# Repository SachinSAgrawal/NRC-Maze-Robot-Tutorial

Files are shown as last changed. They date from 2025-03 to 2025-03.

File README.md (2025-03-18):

# NRC Maze Robot Tutorial

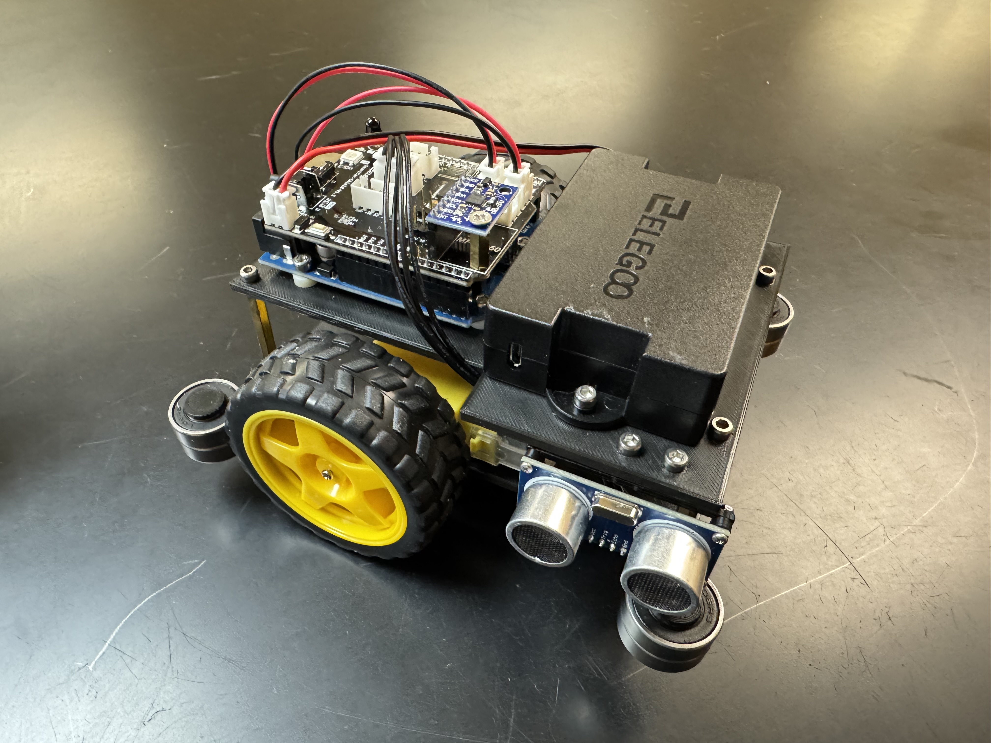
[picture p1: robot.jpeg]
robot


## About
I was going to participate in the National Robotics Challenge as part of my high school’s Engineering Team, which I lead until something happened. However, I am making this tutorial under the CC BY-NC-ND license so that the designs and code are accessible to anyone. If you used this tutorial or found it helpful, I would appreciate if you starred it or even shared it with your friends.

## Competition
The [National Robotics Challenge](https://www.thenrc.org/) takes place each Spring in Marion, Ohio. There are multiple different contests with different levels of difficulty. This tutorial is specifically for the Robot Maze Contest, which involves building and programming a robot to navigate a right/left turn maze. The maze is 10 segments by 10 segments, with each segment being 10 inches by 10 inches. However, the internal navigable is 9.25 inches because the walls have width. The robot must be no larger than 7x7x7 inches and must be completely autonomous (no remote controls or tethers). It must be in contact with the ground at all times and has up to five minutes to complete a run, where faster is better.

## Robot Information
This robot meets those design criteria, and uses an Arduino Uno as it's microcontroller. It can basically be made out of parts from the [ELEGOO Smart Robot Car Kit V4.0](https://www.amazon.com/ELEGOO-Tracking-Ultrasonic-Intelligent-Educational/dp/B07KPZ8RSZ), with everything else being 3D printed or quite inexpensive. The robot moves forward through each segment one at a time, which ensures that it is centered before executing a turn. When it does execute a turn, wherever possible, it moves forward until it is square with the wall and then backs up to do the turn. This realignment functionality helps minimize drift. The robot also checks if all turns are accurate using the MPU, and if that is not the case, then the robot self-corrects. For long stretches of wall that are on the right side of the robot, it can use a PD controller to hug that wall.

## Code Explanation
The only function that is not used is the `mpuAngles` one, which prints all three axes to Serial. Other than that, every line of the code is necessary for the robot to work properly. The first part of the code handles all the variable definitions, followed by the `setup` for things like pin modes. Then there is the main `loop` function, which detects if the button is pressed, and if so, starts doing the maze logic. The rest of it is organized into a bunch of sections with each section containing a few related helper functions for moving, reading from sensors, etc. This is also where the PD controller and check turn function live. The code is fully commented, so you should have no trouble understanding it, and if you can't, then your coding skills are probably not good enough to be competing in the first place.

## Robot Tutorial
Print out the top plate, bottom plate, bearing stoppers, and both ultrasonic mounts according to the specified [print settings](printSettings.md). All five files are in the `printedParts` folder, as well as on both [Printables](https://www.printables.com/model/1232178) and [Thingiverse](https://www.thingiverse.com/thing:6981409). Then, check out the [parts list](partsList.md) and make sure you have everything else. Next, read the [instructions](instructions.md) to assemble your robot. Lastly, upload the [code](mazeCode/mazeCode.ino) onto the Arduino to finish your robot. It is currently set to the maze layout for 2025. However, it is really easy to modify. It basically works like block coding, where you just need to call each function sequentially to have the robot move forward through one segment or turn.

## Notes

### Pictures
This tutorial currently does not include any pictures besides the ones in the parts list and at the top of this file. I will update it with them as soon as possible so that it is easier to follow.

### Crediting
As part of the license included in this repository (see below), you must credit me in your Engineer's Notebook. It would be dishonest and unethical to pass this off as your own because you didn't do the work.

### LED
The LED on the shield indicates the status of the robot. It will be red while the robot is getting set up and turn green once the robot is ready. It is super important to not move the robot in that time, as the MPU is being calibrated. Once the code is finished running, the LED will turn white. While it is moving, the LED will be yellow, teal, or purple if it is going forward, turning, or waiting, respectively. Once the code has run once, it must be reset using the button to run it again.

## Contributors
Sachin Agrawal: I'm a self-taught programmer who knows many languages and I'm into app, game, and web development. For more information, check out my website or Github profile. If you would like to contact me, my email is [github@sachin.email](mailto:github@sachin.email).

## License
This package is licensed under the [Creative Commons BY-NC-ND License](LICENSE.txt). For more information, please visit their [website](https://creativecommons.org/share-your-work/use-remix/cc-licenses/#by-nc-nd). I am only giving everyone permission to edit the layout of the maze since it changes each year, and delay timings as needed. Otherwise, please respect the No Derivatives part of the license and do not alter any of the remaining code. This means that you are not allowed to put this code into ChatGPT to change it in any way. This also means that you cannot write a library to try to shorten this code because, on top of being a bad idea, you are actually making the code longer, but splitting it across multiple files. It is also prohibited to modify any of the printed parts, including removing my name from the top plate. Unless I have explicitly given you permission in writing to make more modifications, what is said here takes precedence in terms of licensing.

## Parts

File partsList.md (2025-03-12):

# Parts List

ELEGOO Smart Robot Car Kit V4.0: https://www.amazon.com/ELEGOO-Tracking-Ultrasonic-Intelligent-Educational/dp/B07KPZ8RSZ

| Name | Quantity | Image | Status | Link | Reference | Docs | Pinout | Shield |
|---|---|---|---|---|---|---|---|---|
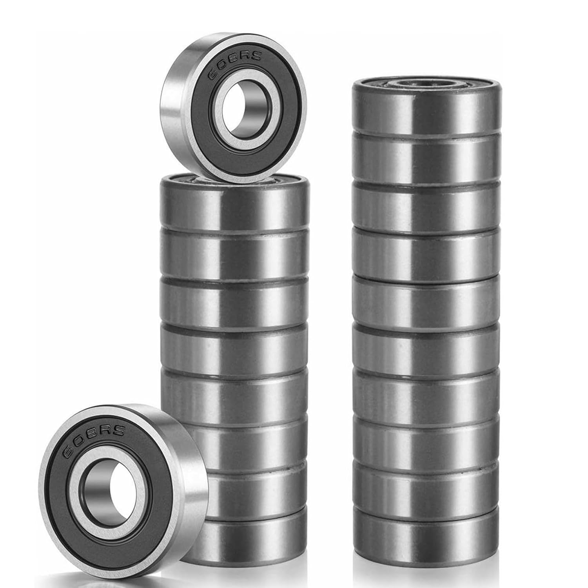
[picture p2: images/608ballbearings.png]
| 608 Ball Bearings | 1 pack of 25 |  | Separate | [Amazon](https://www.amazon.com/YAMASO-Pcs-608-Ball-Bearings/dp/B0CYYYZRV9) | | | | |
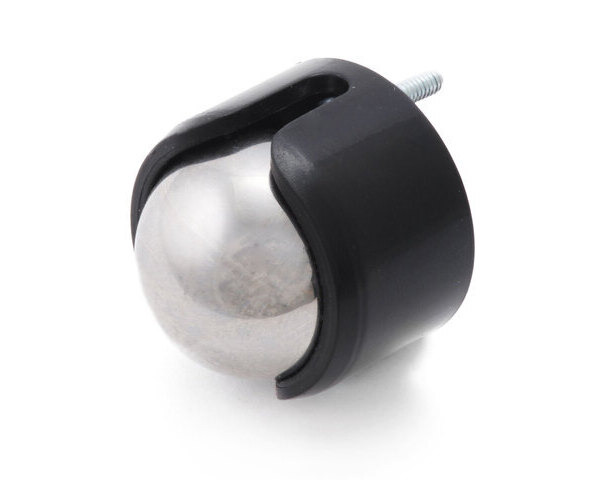
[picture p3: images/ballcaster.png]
| Ball Caster with 3/4″ Metal Ball | 1 |  | Separate | [Pololu](https://www.pololu.com/product/955) | Holes 15mm apart | | | |
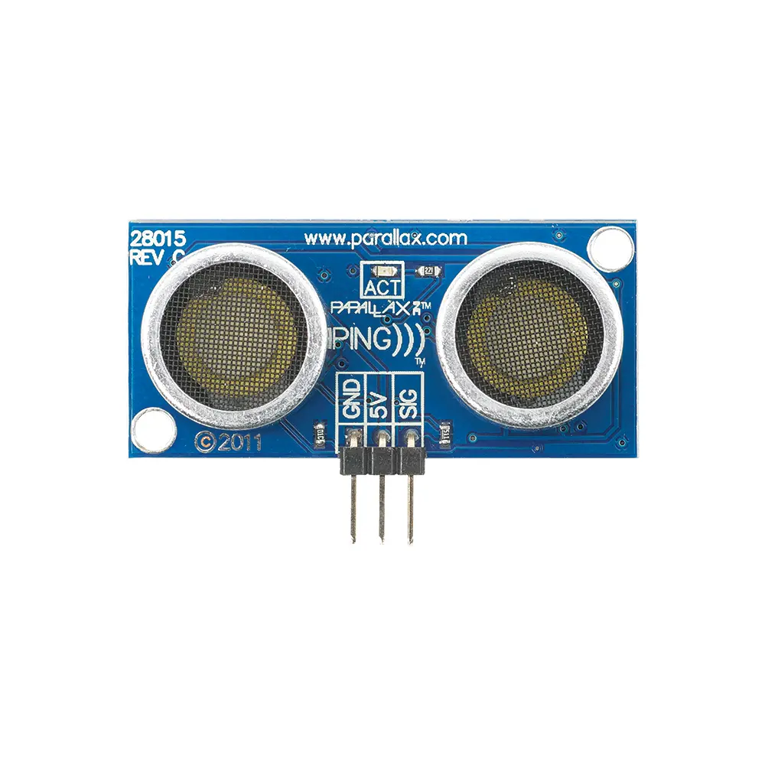
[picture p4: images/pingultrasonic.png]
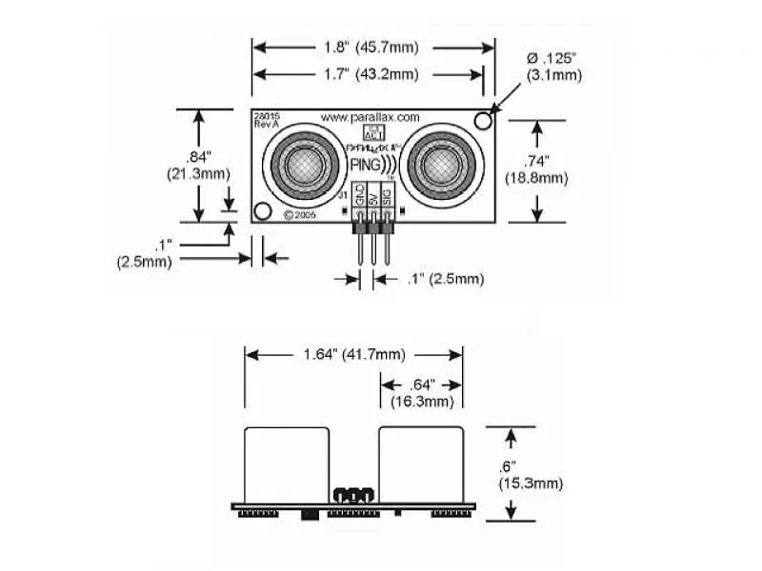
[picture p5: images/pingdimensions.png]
| Parallax Ping))) Ultrasonic Sensor  | 1 |  | Separate | [Parallax](https://www.parallax.com/product/ping-ultrasonic-distance-sensor/) |  | [Arduino](https://docs.arduino.cc/built-in-examples/sensors/Ping/) | Gnd, 5V, Signal | Servo2 |
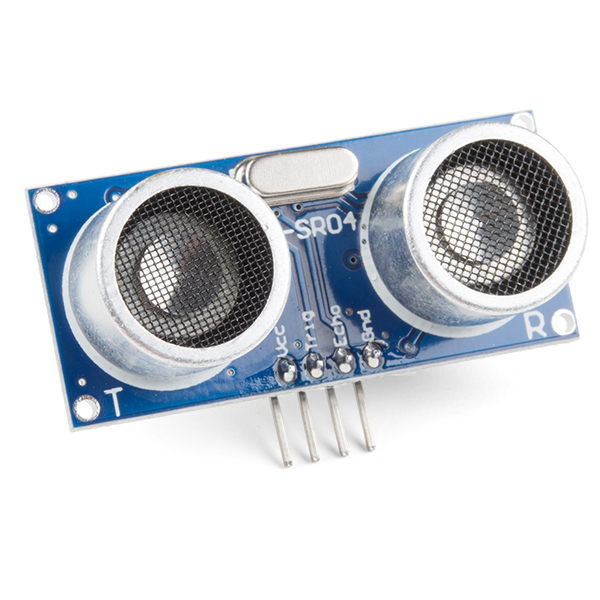
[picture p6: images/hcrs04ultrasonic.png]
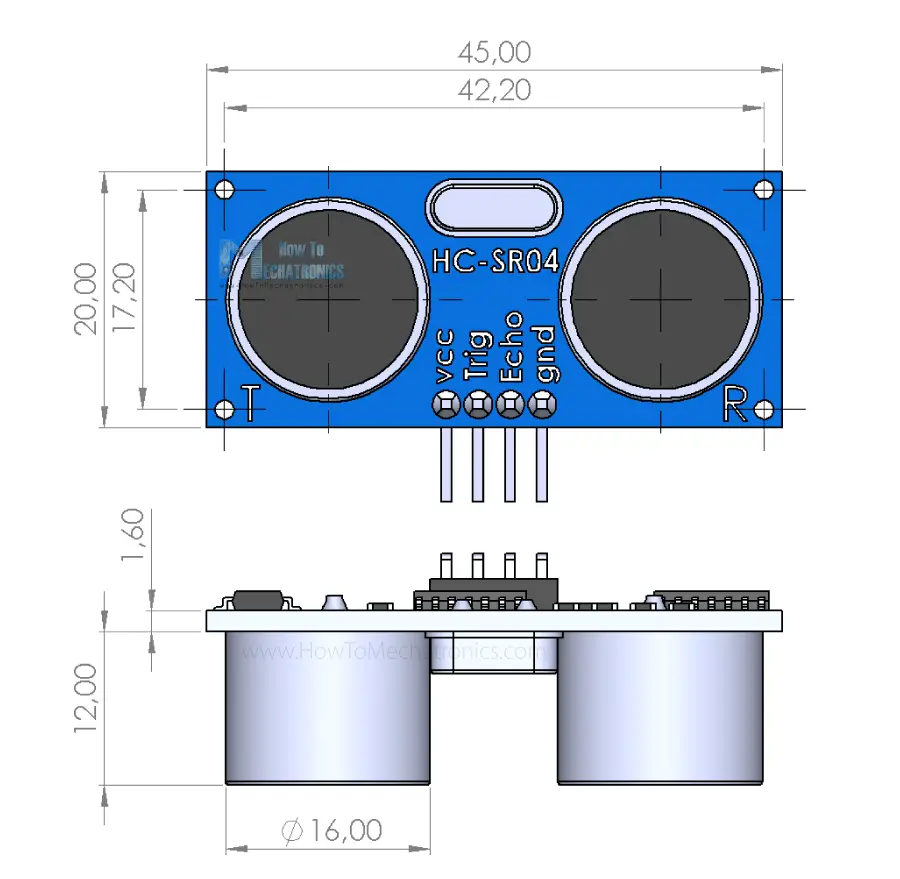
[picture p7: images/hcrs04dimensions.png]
| HC SR04 Ultrasonic Sensor | 1 |  | From Elegoo Kit | |   | | Vcc, Trig (Digital), Echo (Digital), Gnd | US |
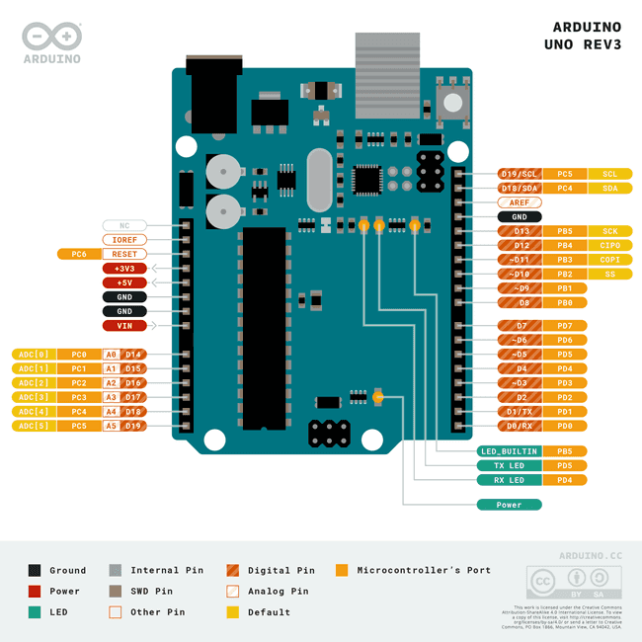
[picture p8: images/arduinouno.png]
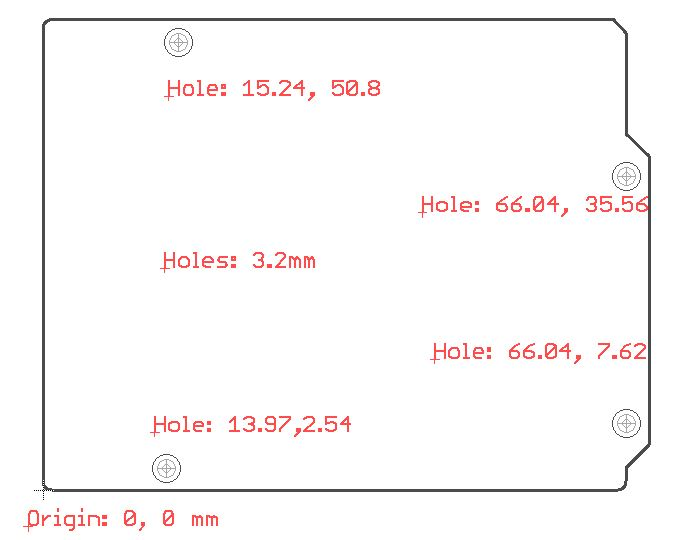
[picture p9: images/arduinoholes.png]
| Arduino Uno | 1 |  | From Elegoo Kit | |  | | | |
| Smart Robot Car Kit Shield | 1 |  | From Elegoo Kit | | | [Google Drive](https://drive.google.com/drive/folders/1OGWDPXKMALmwXZrCxrwO-zCWzvXuK-5q) | | |
| MPU 6050 Gyroscope | 1 |  | From Elegoo Kit | |  | | Vcc, Gnd, SCL, SDA | MPU |
| TT DC Gearbox Motor | 2 |  | From Elegoo Kit | | | | Pos, Neg | M1 & M2  |
| Rubber Tire and Wheel | 2 |  | From Elegoo Kit | | | | | |
| Battery Pack with JST Connector | 1 |  | From Elegoo Kit | | Holes 78mm apart | | Vin, Gnd | Power_In |
| M3 40mm Threaded Hexagon Spacers | 4 |  | From Elegoo Kit | | | | | |
| M3 Hex Nuts | 15 |  | From Elegoo Kit | | | | | |
| Aluminum Blocks | 2 |  | From Elegoo Kit | | | | | |
| M3 10mm Hex Screws | 16 |  | From Elegoo Kit | | | | | |
| M3 12mm Hex Screws | 2 |  | From Elegoo Kit | | | | | |
| M3 14mm Hex Screws | 5 |  | From Elegoo Kit | | | | | |
| M3 30mm Hex Screws | 4 |  | From Elegoo Kit | | | | | |
| Separation Pillars | 5 |  | From Elegoo Kit | | | | | |
| M3 5mm Countersunk Screws | 2 |  | From Elegoo Kit | | | | | |
| M3 11mm Copper Pillar | 1 |   | From Elegoo Kit | | | | | |
| M1.6 8mm Screws | 4 |  | From Elegoo Kit | | | | | |
| M1.6 Nuts | 4 |  | From Elegoo Kit | | | | | |
| M2 25mm Self-Tapping Screws | 2 |  | From Elegoo Kit | | | | | |
| 4 Pin JST Cable | 1 |  | From Elegoo Kit | | | | | |
| 3 Pin Jumper | 1 |  | Separate | | | | | |
| Top Plate | 1 |  | 3D Print | | | | | |
| Bottom Plate | 1 |  | 3D Print | | | | | |
| Bearing Stoppers | 4 |  | 3D Print | | | | | |
| Ultrasonic Mount 1 | 1 |  | 3D Print | | | | | |
| Ultrasonic Mount 2 | 1 |  | 3D Print | | | | | |

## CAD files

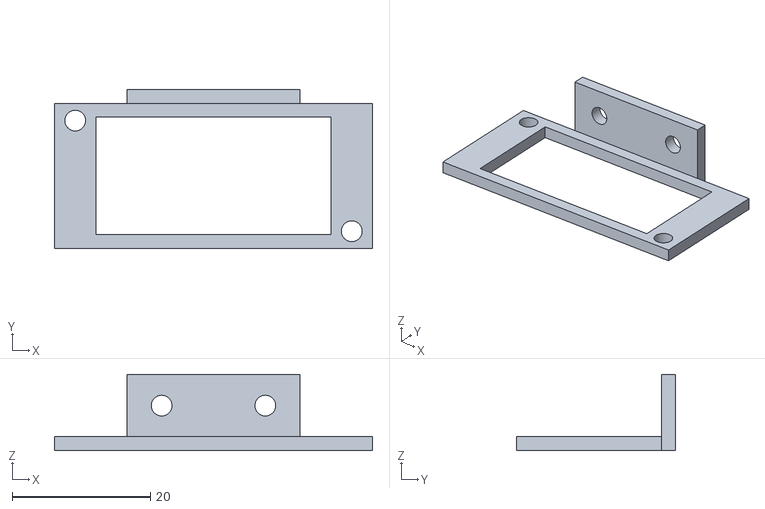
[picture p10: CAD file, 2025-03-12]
printedParts/ultrasonicmount1.stl
46.0 x 23.0 x 11.0

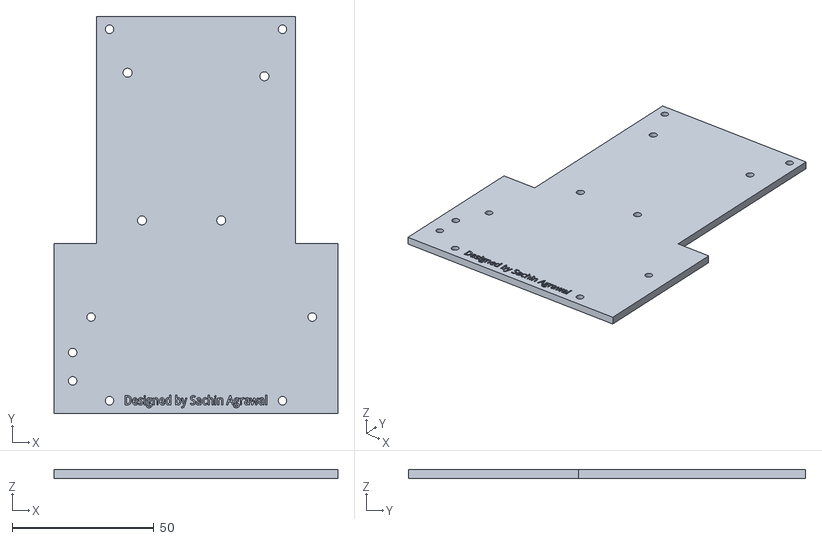
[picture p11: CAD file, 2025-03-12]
printedParts/topplate.stl
100.0 x 140.0 x 3.00

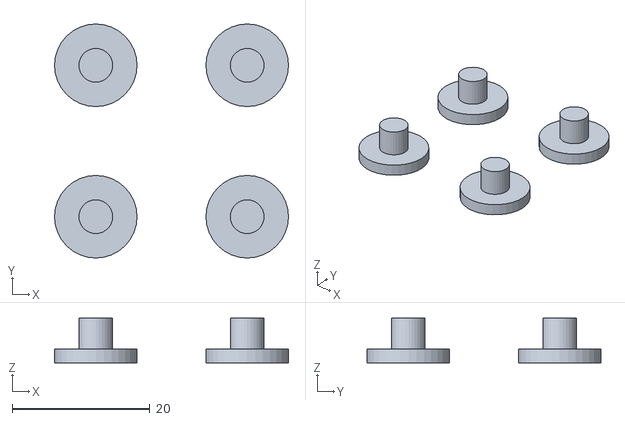
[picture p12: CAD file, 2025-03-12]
printedParts/bearingstoppers.stl
34.0 x 34.0 x 6.50

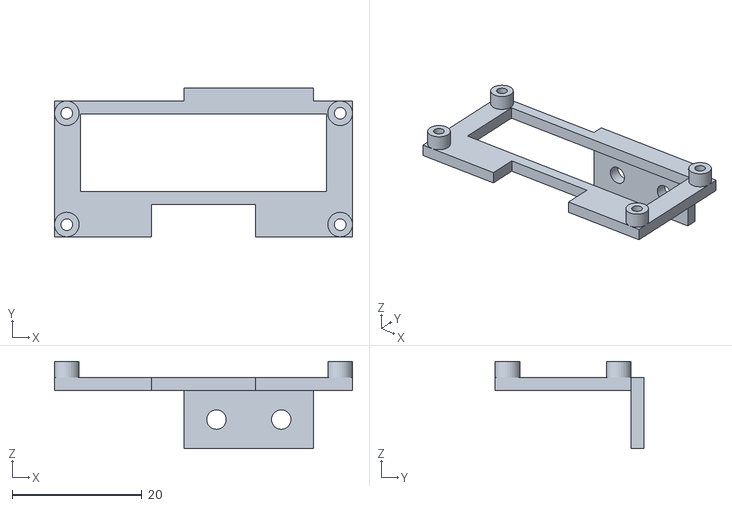
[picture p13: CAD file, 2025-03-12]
printedParts/ultrasonicmount2.stl
46.0 x 23.0 x 13.5

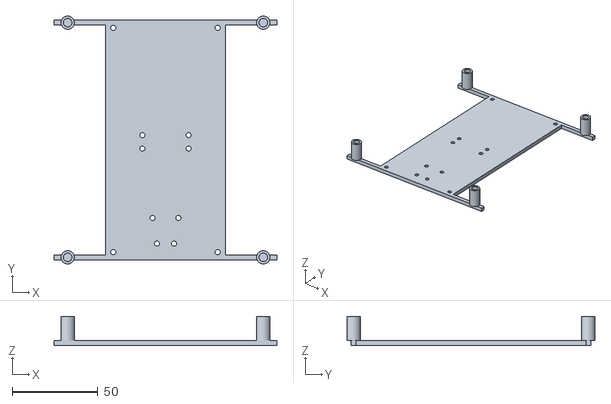
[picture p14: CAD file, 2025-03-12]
printedParts/bottomplate.stl
130.0 x 144.8 x 17.0

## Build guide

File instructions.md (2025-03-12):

# Instructions

## Step 1
Slide two bearings onto each of the four posts on the bottom plate.

## Step 2
Apply a little bit of super glue to the bearing stoppers and attach them to the tops of the bearing holders to prevent the bearings from sliding out if the robot is turned upside down.

## Step 3
Screw the aluminum mounting blocks onto the motors using two M3 30mm screws and two M3 hex nuts. Repeat this twice.

## Step 4
Attach both motors onto the bottom plate using four M3 10mm screws. 

## Step 5
Screw the ball caster into the bottom plate using the nuts/bolts that came with it, then slide the metal ball into the caster.

## Step 6
Screw the Ping ultrasonic sensor into the first mount using two M3 14mm screws with two separation pillars and two M3 hex nuts.

## Step 7
Attach that assembly to the bottom plate using two M3 10mm screws and two M3 hex nuts. 

## Step 8
Screw the HC-SR04 ultrasonic sensor into the second mount using four M1.6 8mm screws and four M1.6 nuts.

## Step 9
Attach that assembly to the top plate using two M3 10mm screws and two M3 hex nuts. 

## Step 10
Screw the battery pack into the top plate using two M3 12mm screws and two M3 hex nuts. 

## Step 11
Screw the Arduino Uno to the top plate using three M3 14mm screws with three separation pillars and three M3 hex nuts.

## Step 12
Attach the MPU to the shield, then screw it in place using the M3 5mm countersunk screws and M3 11mm copper pillar.

## Step 13
Attach the shield to Arduino by sliding it on.

## Step 14
Screw the M3 40mm spacers to the bottom plate using four M3 10mm screws.

## Step 15
Attach the top plate to the tops of the spacers using four M3 10mm screws.

## Step 16
Connect all of the wires according to the `Shield` column in the [parts list](partsList.md).

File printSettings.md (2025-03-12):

# Print Settings

I printed all parts on a Prusa i3 MK3S+, but any printer with good tolerances should work. Depending on how well your bed adhesion is, you may or may not want to add glue, especially for the top and bottom plates.

## All Parts
- 3 Perimeters
- 50% Infill 
- Gyroid Pattern
- 0.2mm Layer Height

## Part Specific

### Top Plate
- No Supports Needed
- Brim Enabled

### Bottom Plate
- Support (on build plate only)
- Brim Enabled

### Ultrasonic Mount 1
- No Supports Needed
- Brim Optional

### Ultrasonic Mount 2
- Support (on build plate only)
- Brim Enabled

### Bearing Stoppers
- No Supports Needed
- Brim Disabled

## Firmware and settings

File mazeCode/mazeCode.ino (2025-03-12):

// VARIABLES

// How long to wait after each instruction
int delayLength = 500;

// How long to make a 90 degree turn
int turnNinetyL = 350;
int turnNinetyR = 350;

// How long to go forward 10 inches
int forwardTenIn = 450;

// How long to hit into wall to realign
int forwardToClear = 250;

// How far to back up after realigning
int backFromRealign = 150;

// DEFINITIONS

// Button
#define button 2
boolean buttonState;
boolean buttonPressed;
boolean codeHasRun = false;

// RGB LED
#include "FastLED.h"
#define PIN_RBGLED 4
#define NUM_LEDS 1
CRGB leds[NUM_LEDS];

// Needed for LED but do not understand it fully
uint32_t Color(uint8_t r, uint8_t g, uint8_t b) {
  return (((uint32_t)r << 16) | ((uint32_t)g << 8) | b);
}

// Front Ultrasonic
const int pingPin = 11;
long durationF;
float distanceF;

// Right Ultrasonic
const int trigPinR = 13;
const int echoPinR = 12;
long durationR;
float distanceR;

// MPU6050
#include "Wire.h"
#include <MPU6050_light.h>
MPU6050 mpu(Wire);
float angZ = 0;

// DC motors
#define PWMA 5
#define PWMB 6
#define BIN1 7
#define AIN1 8
#define STBY 3

// Robot Speed
int speedMed = 125; 
int speedFast = speedMed + 50; 
int speedSlow = speedMed - 50;
int motorACorrection = 4;

// PD Controller
#define goalR 2 // 2 inches away from right wall
const float Gp = 30.0; 
const float Gd = 60.0;
int leftPWM = speedMed;
int rightPWM = speedMed;
float errorP; // Proportional error
float errorD; // Derivative error
float initialPoint; 
float finalPoint;

// Important setup function
void setup() {
  // Set up the LED
  FastLED.addLeds<NEOPIXEL, PIN_RBGLED>(leds, NUM_LEDS);
  FastLED.setBrightness(10); // Don't increase because it gets too bright

  // Warning during setup
  FastLED.showColor(Color(255, 1, 1)); // Red

  // Start communication with the serial monitor
  Serial.begin(9600);

  // Enable the right ultrasonic sensor
  pinMode(trigPinR, OUTPUT); 
  pinMode(echoPinR, INPUT);

  // Set up the button pin
  pinMode(button, INPUT_PULLUP); 

  // Set up the DC motors
  pinMode(PWMA, OUTPUT);
  pinMode(PWMB, OUTPUT);
  pinMode(AIN1, OUTPUT);
  pinMode(BIN1, OUTPUT);
  pinMode(STBY, OUTPUT);

  // Set the initial motor speed
  motorSpeed(speedSlow);

  // Set up the MPU
  Wire.begin();
  byte status = mpu.begin();
  Serial.print(F("MPU6050 status: "));
  Serial.println(status);
  while(status!=0){ } // Stop everything if could not connect to it
  Serial.println("Calculating offsets, do not move MPU6050");
  delay(1000);
  mpu.calcOffsets(); // Gyro and accelerometer
  Serial.println("Ready");

  // Setup complete
  FastLED.showColor(Color(1, 255, 1)); // Green
}

// Important loop function
void loop() {
  // Determine whether the button is pressed
  buttonState = digitalRead(button);

  if (buttonState == 0) {
    // Button has been pressed
    FastLED.showColor(Color(1, 1, 255)); // Blue

    // Can execute main logic if it is not already run
    if (!codeHasRun) {
      // WEEEEEE
      mazelogic2025();

      codeHasRun = true;
      Serial.println("Code Has Run");
      FastLED.showColor(Color(255, 255, 255)); // White
    }
  } else if (codeHasRun) {
    // Code has run once before
    FastLED.showColor(Color(255, 255, 255)); // White
  }
}

// Functions for the logic of the different mazes 

// Full 100'x100' maze
void fullMazeLogic() {
  // =========
  // EDIT THIS
  // =========
}

// The maze layout from 2025
void mazelogic2025() {
  tenInForward();
  tenInForward();
  tenInForward();
  // 4
  turnLeft();
  tenInForward();
  tenInForward();
  // 6
  turnLeft();
  tenInForward();
  // 7
  turnRight();
  tenInForward();
  // 8
  turnLeft();
  tenInForward();
  // 9
  turnRight();
  tenInForward();
  // 10
  turnRight();
  tenInForward();
  tenInForward();
  // 12
  ninetyRight();
  tenInForward();
  // 13
  turnLeft();
  tenInForward();
  // 14
  turnRight();
  tenInForward();
  tenInForward();
  tenInForward();
  // 17
  turnLeft();
  tenInForward();
  tenInForward();
  // 19
  turnLeft();
  tenInForward();
  tenInForward();
  tenInForward();
  // 22
  ninetyRight();
  tenInForward();
  tenInForward();
  // 24
  ninetyLeft();
  tenInForward();
  tenInForward();
  // 26
  turnLeft();
  tenInForward();
  tenInForward();
  // 28
  turnRight();
  tenInForward();
  // 29
  turnLeft();
  tenInForward();
  // 30
  turnRight();
  tenInForward();
  // 31
  turnLeft();
  tenInForward();
  // 32
  turnRight();
  tenInForward();
  // 33
  turnRight();
  tenInForward();
  hugWallUntil(12);
  tenInForward();
  // 38
  turnLeft();
  tenInForward();
  // 39
  turnLeft();
  hugWallUntil(2);
}

// Functions to continuously update the MPU when the robot is moving

// Actual logic
void dddelay(int dTime) {
  long currTime = millis();
  while (millis() - currTime < dTime) {
    mpu.update();
    angZ = mpu.getAngleZ();
    delay(5);
  }
}

// Also update LED
void ddelay(int dTime) {
  FastLED.showColor(Color(255, 1, 255)); // Magenta
  dddelay(dTime);
  FastLED.showColor(Color(0, 0, 0)); // Off
}

// Functions to set the motor speed

// Set both speeds
void motorSpeed(int speed) {
  int constrainedSpeed = constrain(speed, speedSlow, speedFast);
  motorASpeed(constrainedSpeed);
  motorBSpeed(constrainedSpeed);
}

// Independently set X
void motorASpeed(int speed) {
  analogWrite(PWMA, speed + motorACorrection);
}

// Independently set Y
void motorBSpeed(int speed) {
  analogWrite(PWMB, speed);
}

// Functions to have the robot move in a certain direction for a specified time

// Forward
void moveForward(int milliseconds) {
  FastLED.showColor(Color(255, 255, 1)); // Yellow
  digitalWrite(STBY, HIGH);
  digitalWrite(AIN1, HIGH);
  digitalWrite(BIN1, HIGH);
  // Ease in and out for longer distances
  if (milliseconds == forwardTenIn) {
    for (int i = 0; i <= 25; i++) {
      motorSpeed(speedSlow + 2 * i);
      dddelay(5);
    }
    motorSpeed(speedMed);
    dddelay(milliseconds - 250);
    for (int i = 0; i <= 25; i++) {
      motorSpeed(speedMed - 2 * i);
      dddelay(5);
    }
  } else {
    dddelay(milliseconds);
  }
  motorSpeed(speedSlow);
  FastLED.showColor(Color(0, 0, 0)); // Off
  digitalWrite(STBY, LOW);
}

// Backward
void moveBackward(int milliseconds) {
  FastLED.showColor(Color(255, 255, 1)); // Yellow
  digitalWrite(STBY, HIGH);
  digitalWrite(AIN1, LOW);
  digitalWrite(BIN1, LOW);
  dddelay(milliseconds);
  FastLED.showColor(Color(0, 0, 0)); // Off
  digitalWrite(STBY, LOW);
}

// Left
void moveLeft(int milliseconds) {
  FastLED.showColor(Color(1, 255, 255)); // Teal
  digitalWrite(STBY, HIGH);
  digitalWrite(AIN1, LOW);
  digitalWrite(BIN1, HIGH);
  dddelay(milliseconds);
  FastLED.showColor(Color(0, 0, 0)); // Off
  digitalWrite(STBY, LOW);
}

// Right
void moveRight(int milliseconds) {
  FastLED.showColor(Color(1, 255, 255)); // Teal
  digitalWrite(STBY, HIGH);
  digitalWrite(AIN1, HIGH);
  digitalWrite(BIN1, LOW);
  dddelay(milliseconds);
  FastLED.showColor(Color(0, 0, 0)); // Off
  digitalWrite(STBY, LOW);
}

// Turning functions that realign the robot each time

// Align and turn left
void turnLeft() {
  // Move forward until it hits the wall
  Serial.println("Forward");
  moveForward(forwardToClear);
  ddelay(delayLength);

  // Back up a little to clear the turn
  Serial.println("Back");
  moveBackward(backFromRealign);
  ddelay(delayLength);

  // Get the goal value to pass into function below
  mpu.update();
  float initAngle = mpu.getAngleZ();
  Serial.print("AngZ: ");
  Serial.println(initAngle);

  // Execute the actual turn
  Serial.println("Left");
  moveLeft(turnNinetyL);
  ddelay(delayLength);  

  // Check if the turn is accurate using goal
  Serial.println("Check Turn");
  checkAccurateTurn(initAngle, true, false);
  ddelay(delayLength);
}

// Align and turn right
void turnRight() {
  // Move forward until it hits the wall
  Serial.println("Forward");
  moveForward(forwardToClear);
  ddelay(delayLength);

  // Back up a little to clear the turn
  Serial.println("Back");
  moveBackward(backFromRealign);
  ddelay(delayLength);

  // Get the goal value to pass into function below
  mpu.update();
  float initAngle = mpu.getAngleZ();
  Serial.print("AngZ: ");
  Serial.println(initAngle);

  // Execute the actual turn
  Serial.println("Right");
  moveRight(turnNinetyR);
  ddelay(delayLength);

  // Check if the turn is accurate using goal
  Serial.println("Check Turn");
  checkAccurateTurn(initAngle, false, true);
  ddelay(delayLength);
}

// Turning functions that do not reset the robot each time

// Left 90 degrees
void ninetyLeft() {
  // Get the goal value to pass into function below
  mpu.update();
  float initAngle = mpu.getAngleZ();
  Serial.print("AngZ: ");
  Serial.println(initAngle);

  // Execute the actual turn
  Serial.println("Left 90 Deg");
  moveLeft(turnNinetyL);
  ddelay(delayLength);  

  // Check if the turn is accurate using goal
  Serial.println("Check Turn");
  checkAccurateTurn(initAngle, true, false);
  ddelay(delayLength);
}

// Right 90 degrees
void ninetyRight() {
  // Get the goal value to pass into function below
  mpu.update();
  float initAngle = mpu.getAngleZ();
  Serial.print("AngZ: ");
  Serial.println(initAngle);

  // Execute the actual turn
  Serial.println("Right 90 Deg");
  moveRight(turnNinetyR);
  ddelay(delayLength);  

  // Check if the turn is accurate using goal
  Serial.println("Check Turn");
  checkAccurateTurn(initAngle, false, true);
  ddelay(delayLength);
}

// Functions to just move forward/backward

// Move forward 10 inches through one maze segment
void tenInForward() {
  Serial.println("Forward 10in");
  moveForward(forwardTenIn);
  ddelay(delayLength);
}

// Move forward until a certain distance from front wall
void forwardUntil(int inches) {
  float distFromFrontWall;
  do {
    distFromFrontWall = frontUltrasonic();
    moveForward(50);
  } while (distFromFrontWall > inches);
  ddelay(delayLength);
}

// Move backward 10 inches through one maze segment
void tenInBackward() {
  Serial.println("Backward 10in");
  moveForward(forwardTenIn);
  ddelay(delayLength);
}

// Functions that can be called to easily read the ultrasonic sensors

// Front ultrasonic
float frontUltrasonic() {
  pinMode(pingPin, OUTPUT);
  digitalWrite(pingPin, LOW);
  delayMicroseconds(2);
  digitalWrite(pingPin, HIGH);
  delayMicroseconds(5);
  digitalWrite(pingPin, LOW);
  pinMode(pingPin, INPUT);
  durationF = pulseIn(pingPin, HIGH);
  distanceF = microsecondsToInches(durationF);
  Serial.print("DisF: ");
  Serial.println(distanceF, 2);
  return distanceF;
}

// Right ultrasonic
float rightUltrasonic() {
  digitalWrite(trigPinR, LOW);
  delayMicroseconds(2);
  digitalWrite(trigPinR, HIGH);
  delayMicroseconds(10);
  digitalWrite(trigPinR, LOW);
  durationR = pulseIn(echoPinR, HIGH);
  distanceR = durationR * 0.034 / 2.0 / 2.54;
  Serial.print("DisR: ");
  Serial.println(distanceR, 2);
  return distanceR;
}

// Ping conversion
long microsecondsToInches(long microseconds) {
  return microseconds / 74 / 2;
}

// Functions related to hugging aka staying a certain distance away from the right wall

// PD controller to move motors accordingly
void hugWall() {
  // Read and print the output of the right sensor
  Serial.println(" ");
  float distFromRightWall = rightUltrasonic();
  finalPoint = distFromRightWall; 

  // Just move straight if distance is greater than 200
  if (distFromRightWall > 200) {
    Serial.println("Going straight");
    motorSpeed(speedMed);
    moveForward(15);
    ddelay(10);
    return;
  }

  // Calculate and print the proportional and derivative errors
  errorP = distFromRightWall - goalR;  // Positive if too far and negative if too close to wall (should ideally be 0, with max of 2 and min of -2)
  errorD = finalPoint - initialPoint;  // Positive if heading away and negative if going towards wall (should be 0, with very slight variances)

  // Print the errors to the serial monitor
  Serial.print("ErrP: ");
  Serial.println(errorP);
  Serial.print("ErrD: ");
  Serial.println(errorD);

  // Print finalPoint and initialPoint to check if updating correctly
  Serial.print("Final: ");
  Serial.println(finalPoint, 2);
  Serial.print("Initl: ");
  Serial.println(initialPoint, 2);

  // Use proper math to calculate the wheel speed and print it
  leftPWM = (rightPWM + errorP * Gp + errorD * Gd);
  leftPWM = constrain(leftPWM, speedSlow, speedFast);
  Serial.print("lPWM: ");
  Serial.println(leftPWM);
  Serial.print("rPWM: ");
  Serial.println(rightPWM);

  // Actually move the wheels at that speed
  motorASpeed(rightPWM);
  motorBSpeed(leftPWM);
  moveForward(15);

  // Update the memory value
  initialPoint = finalPoint;

  ddelay(10);
}

// Hug the wall for a set amount of times
void hugWallfor(int count) {
  for (int i = 0; i < count; i++) {
    hugWall();
  }
  motorSpeed(speedSlow);
  ddelay(delayLength);
}

// Hug the wall until a certain distance from front wall
void hugWallUntil(int inches) {
  float distFromFrontWall;
  do {
    distFromFrontWall = frontUltrasonic();
    hugWall();
  } while (distFromFrontWall > inches);
  motorSpeed(speedSlow);
  ddelay(delayLength);
}

// Functions related to the MPU6050 gyroscope

// Print the MPU data to the serial monitor
void mpuAngles() {
  // Get angle variables
  mpu.update();
  float angX = mpu.getAngleX();
  float angY = mpu.getAngleY();
  float angZ = mpu.getAngleZ();

  // Print them
  Serial.print("X : ");
	Serial.print(angX);
	Serial.print("\tY : ");
	Serial.print(angY);
	Serial.print("\tZ : ");
	Serial.println(angZ);
}

// Check if the robot has turned the full 90 degrees and finish turning as needed
void checkAccurateTurn(float originalAngle, bool leftTurn, bool rightTurn) {
  // Calculate the angles
  float targetAngle = 0;

  if (leftTurn && !rightTurn) {
    targetAngle = originalAngle + 90;
  } else if (rightTurn && !leftTurn) {
    targetAngle = originalAngle - 90;
  }

  float tolerance = 1;
  float goalMore = targetAngle + tolerance;
  float goalLess = targetAngle - tolerance;

  // Print the angles
  Serial.print("Goal: ");
  Serial.println(targetAngle);
  Serial.print("Less: ");
  Serial.println(goalLess);
  Serial.print("More: ");
  Serial.println(goalMore);
  Serial.print("CurZ: ");
  Serial.println(angZ);

  // Maximum correction attempts
  int attempt = 0;
  const int maxAttempts = 30; 

  // Determine if the robot is basically facing the right direction
  if (angZ < goalMore) {
    // Too far left
    while ((angZ > goalMore || angZ < goalLess) && attempt < maxAttempts) {
      moveLeft(10);
      Serial.print("Slight Left: ");
      Serial.println(angZ);
      ddelay(50);
      attempt++;
    }
  } else if (angZ > goalLess) {
    // Too far right
    while ((angZ > goalMore || angZ < goalLess) && attempt < maxAttempts) {
      moveRight(10);
      Serial.print("Slight Right: ");
      Serial.println(angZ);
      ddelay(50);
      attempt++;
    }
  }

  // Break if reached the maximum attempt count
  if (attempt >= maxAttempts) {
    Serial.println("Max correction attempts reached.");
  } else {
    Serial.println("Angle Fine");
  }
}
